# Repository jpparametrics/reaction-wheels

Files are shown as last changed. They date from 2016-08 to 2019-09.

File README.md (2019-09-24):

# THIS REPO IS NO LONGER USED. CHECK ORESAT-STRUCTURE REPO FOR CURRENT REACTION WHEEL FILES
# CubeSAT-Reaction-Wheel

Portland State University is developing Oregon’s first orbital satellite, a 2U Cubesat dubbed Oresat. This cubesat will use a reaction wheel system for attitude control and pointing of the onboard antennas and cameras. I am developing the controller, designing the structure and sourcing hardware for both the space rated system and a ground test system that will also be used for demonstration purposes. This system has been tested using the Dryden Drop Tower at PSU as well as in captive hanging tests. The current controller is a simple proportional controller, however using data collected from the drop test I will refine the model and implement a more sophisticated controller. Video of the tests can be seen at:  [Captive Controller Hanging Test](https://www.youtube.com/watch?v=Is1gPHlewtgand) and [Dryden Drop Tower Micro-Gravity Test](https://www.youtube.com/watch?v=cC2FpmCP5B4)

Both of the previous tests were conducted using a simple open loop proportional controller that was tuned via test to induce a slightly underdamped response. This was to create data that can be more easily compared to an ideal model.

CubeSat Model Comparison

## Ongoing Development

There's a Google drive folder [here](https://drive.google.com/drive/folders/0BzW5XSZ87m-TVnFDZUc1TUkwN1U?usp=sharing)

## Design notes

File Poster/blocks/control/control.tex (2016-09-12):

\documentclass[slidestop,compress]{beamer}
\usepackage[orientation=portrait,size=custom, width=30, height=25, debug]{beamerposter}
\usetheme{simple}

\usepackage{lmodern}
\usepackage[scale=2]{ccicons}

% TODO: 
%   position adjustement
%   change colours
%       

% Watermark background (simple theme)

\begin{document}

\begin{frame}[plain]
\begin{block}{\vspace{0.5 cm} 

\centering Controls Development}
\begin{columns}
	\column{.9\textwidth}
\begin{itemize}
\item The controller for the reaction wheel system is a simple PID loop 
\item The top-level controller design procedure was as follows:
\begin{enumerate}
\item Determine the transfer functions from dynamics analysis of free body diagrams of the system
\item Create simulation in GNU Octave
\item Design the controller using iterative testing (with comparisons to the model) and classical Bode techniques
\end{enumerate}
\item The forces acting on the cube are the torques created by the motors $T_i^0$, damping effects $b_1 \dot{\theta}_{cube}$, and spring effects $G_1 \theta_{cube}$. Summing the moments around the center of gravity gives the following equation (for the x-axis):

\[
\sum M_0^{+ \circlearrowleft} = I_{x,cube} \ddot{\theta}_{x,cube} = T^0_{Ax} + T^0_{Bx} - T^0_{Cx} - T^0_{Dx} + T^0_x - \dot{\theta}_{x,cube} - G_x \theta_{x,cube}.
\] 

\item By setting the system to Standard Equilibrium Position (at SEP the input perturbations are set to zero), considering only a single input, substituting the torque-inertia relation,  and taking the Laplace transform we arrive at the ({\emph{incredibly simple}}) transfer function of the cube:
\[G_A(s)=\frac{\theta_{x,cube}(s)}{\theta_A(s)}=\frac{s^2}{\cfrac{I_{x,cube}}{\sin(45^{\circ}) I_{rw}}s^2 + \cfrac{b_x}{\sin(45^{\circ}) I_{rw}}s + \cfrac{G_x}{\sin(45^{\circ}) I_{rw}}}.
\]
\end{itemize}
\end{columns}

\vspace{0.5 cm}
\end{block}    
\end{frame}

\end{document}

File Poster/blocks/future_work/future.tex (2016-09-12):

\documentclass[slidestop,compress]{beamer}
\usepackage[orientation=portrait,size=custom, width=25, height=8, debug]{beamerposter}
\usetheme{simple}

\usepackage{lmodern}
\usepackage[scale=2]{ccicons}

% TODO: 
%   position adjustement
%   change colours
%       

% Watermark background (simple theme)

\begin{document}

\begin{frame}[plain]
\begin{block}{\vspace{0.5 cm}

\centering Further Work}

\begin{columns}
\column{.9\textwidth}
\begin{itemize}
\item Need more drop-tests: complete Bode diagram to improve dynamical model, further controller design iterations
\item State determination with sensor fusion via Kalman filtering suntracker, magnetometer, and gyroscopes
\end{itemize}
\end{columns}

\vspace{0.5 cm}
\end{block}    
\end{frame}

\end{document}

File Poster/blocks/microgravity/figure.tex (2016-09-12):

\documentclass[slidestop,compress]{beamer}
\usepackage[orientation=portrait,size=custom, width=25, height=26, debug]{beamerposter}
\usetheme{simple}

\usepackage{lmodern}
\usepackage[scale=2]{ccicons}

% TODO: 
%   position adjustement
%   change colours
%       

% Watermark background (simple theme)

\begin{document}

\begin{frame}[plain]
\begin{block}{\vspace{0.5 cm}

\centering $\pmb \mu$-gravity Controls Testing}
\begin{columns}
    \column{.9\textwidth}
\begin{itemize}
\item Bode analysis of cube dynamics in ``space-like" free-fall environment
\item {\it Portland State University's} Dryden Drop Tower facility can access a 1x$10^{-5}$ to $10^{-6}$-g environment for 2.1 s
\item Cube damps roll following a random (25\% duty cycle PWM) perturbing impulse\\

\end{itemize}
\begin{figure}[!ht]
\centering
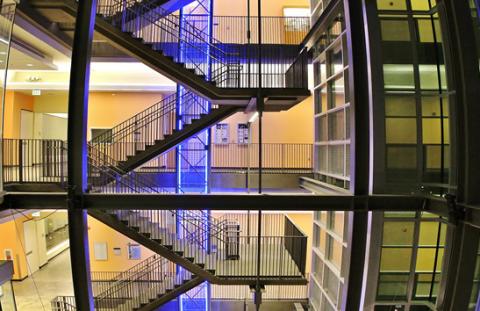
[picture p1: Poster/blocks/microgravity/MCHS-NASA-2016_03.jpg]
{
\caption{{\it Portland State University's} Dryden Drop Tower (Credit: Andrew Wollman)}

\vspace{0.5 cm}
} 
\end{figure}
\end{columns}
\end{block}    
\end{frame}

\end{document}

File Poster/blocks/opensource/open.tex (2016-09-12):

\documentclass[slidestop,compress]{beamer}
\usepackage[orientation=portrait,size=custom, width=25, height=7, debug]{beamerposter}
\usetheme{simple}

\usepackage{lmodern}
\usepackage[scale=2]{ccicons}

% TODO: 
%   position adjustement
%   change colours
%       

% Watermark background (simple theme)

\begin{document}

\begin{frame}[plain]
\begin{block}{\vspace{0.5 cm}

\centering Open-Source}
\begin{columns}
    \column{.9\textwidth}
\begin{itemize}
\item Project deliverables freely and publicly available under a GNU GPL v2 license
\item \texttt{https://github.com/oresat}
\end{itemize}
\end{columns}

\vspace{0.5 cm}
\end{block}    
\end{frame}

\end{document}

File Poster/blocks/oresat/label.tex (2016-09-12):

\documentclass[slidestop,compress]{beamer}
\usepackage[orientation=portrait,size=custom, width=27, height=15, debug]{beamerposter}
\usetheme{simple}

\usepackage{lmodern}
\usepackage[scale=2]{ccicons}

% TODO: 
%   position adjustement
%   change colours
%       

% Watermark background (simple theme)

\begin{document}

\begin{frame}[plain]
\begin{block}{\vspace{0.5 cm}

\centering OreSat}
\begin{columns}
    \column{.9\textwidth}
\begin{itemize}
\item {\bf Mission: STEM outreach by sending live video space-to-ground to tracking stations built and operated by Oregon high schools}
\item Ground stations will be built using 3D printers, COTS WiFi adapter cards, and existing augmented reality cellphone apps that track satellites
\item S-band downlink at approximately 15 dBi gain. Needs to ``point-and-stare" at ground stations with {\bf 5-10$^{\circ}$ of pointing at 1 deg/s of slew}
\item Will use a {\bf{reaction wheel}} based system to provide attitude control

\end{itemize}
\end{columns}

\vspace{0.5 cm}
\end{block}    
\end{frame}

\end{document}

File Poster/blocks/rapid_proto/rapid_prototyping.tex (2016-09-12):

\documentclass[slidestop,compress]{beamer}
\usepackage[orientation=portrait,size=custom, width=25, height=26, debug]{beamerposter}
\usetheme{simple}

\usepackage{lmodern}
\usepackage[scale=2]{ccicons}

% TODO: 
%   position adjustement
%   change colours
%       

% Watermark background (simple theme)

\begin{document}

\begin{frame}[plain]
\begin{block}{\vspace{0.5cm}

\centering Rapid Prototyping}
\begin{columns}
    \column{.9\textwidth}
\begin{itemize}
\item Designed for rapid iteration
\item FDM 3D printed main structure
\item Inexpensive COTS components: DC Brushless hobby motors, Intel Edison microcontroller, and Sparkfun ``blocks"
\item Controller code written in \emph{Python}
\end{itemize}
\begin{figure}[!ht]
\centering
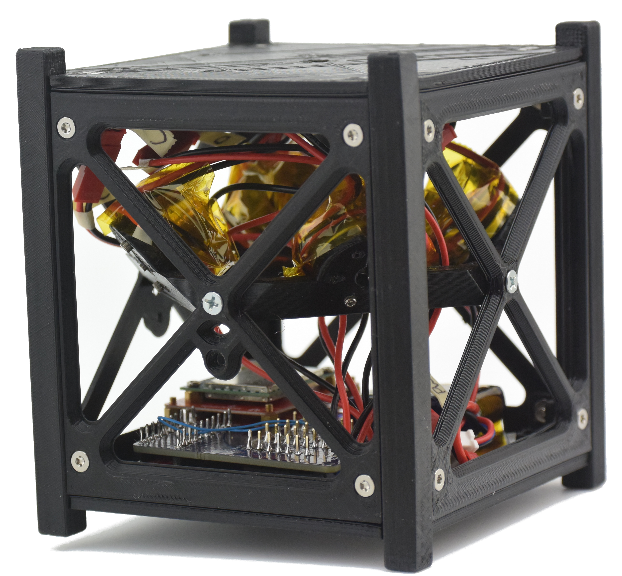
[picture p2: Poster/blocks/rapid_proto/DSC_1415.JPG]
{
\caption{The reaction wheel subsystem test cube.}
} 
\end{figure}
\end{columns}

\vspace{0.5 cm}
\end{block}    
\end{frame}

\end{document}

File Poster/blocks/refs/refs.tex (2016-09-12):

\documentclass[slidestop,compress]{beamer}
\usepackage[orientation=portrait,size=custom, width=25, height=11, debug]{beamerposter}
\usetheme{simple}

\usepackage{lmodern}
\usepackage[scale=2]{ccicons}

% TODO: 
%   position adjustement
%   change colours
%       

% Watermark background (simple theme)

\begin{document}

\begin{frame}[plain]
\begin{block}{\vspace{0.5 cm}

\centering References}
\begin{columns}
    \column{.9\textwidth}
\begin{thebibliography}{9}
\bibitem{Mahoney:15bk}
Mahoney, Erin. {\it CubeSat Launch Initiative: 50 CubeSats from 50 States in 5 Years.} NASA, April 9, 2015. http://www.nasa.gov/content/cubesat-launch-initiative-50-cubesats-from-50-states-in-5-years.\\

\bibitem{Cubesat:14bk}
The CubeSat Program, {\it Cal Poly SLO. CubeSat Design Specification Rev. 13.} San Luis
Obispo: California Polytechnic State University; 2014.
\end{thebibliography}
\end{columns}

\vspace{0.5 cm}
\end{block}    
\end{frame}

\end{document}

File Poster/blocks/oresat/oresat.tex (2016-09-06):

\documentclass[slidestop,compress]{beamer}
\usepackage[orientation=portrait,size=custom, width=11, height=1.1, debug]{beamerposter}
\usetheme{simple}

\usepackage{lmodern}
\usepackage[scale=2]{ccicons}

% TODO: 
%   position adjustement
%   change colours
%       

% Watermark background (simple theme)

\begin{document}

\begin{frame}[plain]
$\mu$-gravity attitude control test    
\end{frame}

\end{document}

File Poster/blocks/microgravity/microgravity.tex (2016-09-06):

\documentclass[slidestop,compress]{beamer}
\usepackage[orientation=portrait,size=custom, width=25, height=20, debug]{beamerposter}
\usetheme{simple}
\usepackage{svg}

\usepackage{lmodern}
\usepackage[scale=2]{ccicons}

% TODO: 
%   position adjustement
%   change colours
%       

% Watermark background (simple theme)

\begin{document}

\begin{frame}[plain]

\includesvg[width=0.9\linewidth]{Gyro_Data_vs_Model_v2}
    
\end{frame}

\end{document}

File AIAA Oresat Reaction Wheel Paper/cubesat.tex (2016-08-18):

% `template.tex', a bare-bones example employing the AIAA class.
%
% For a more advanced example that makes use of several third-party
% LaTeX packages, see `advanced_example.tex', but please read the
% Known Problems section of the users manual first.
%
% Typical processing for PostScript (PS) output:
%
%  latex template
%  latex template   (repeat as needed to resolve references)
%
%  xdvi template    (onscreen draft display)
%  dvips template   (postscript)
%  gv template.ps   (onscreen display)
%  lpr template.ps  (hardcopy)
%
% With the above, only Encapsulated PostScript (EPS) images can be used.
%
% Typical processing for Portable Document Format (PDF) output:
%
%  pdflatex template
%  pdflatex template      (repeat as needed to resolve references)
%
%  acroread template.pdf  (onscreen display)
%
% If you have EPS figures, you will need to use the epstopdf script
% to convert them to PDF because PDF is a limmited subset of EPS.
% pdflatex accepts a variety of other image formats such as JPG, TIF,
% PNG, and so forth -- check the documentation for your version.
%
% If you do *not* specify suffixes when using the graphicx package's
% \includegraphics command, latex and pdflatex will automatically select
% the appropriate figure format from those available.  This allows you
% to produce PS and PDF output from the same LaTeX source file.
%
% To generate a large format (e.g., 11"x17") PostScript copy for editing
% purposes, use
%
%  dvips -x 1467 -O -0.65in,0.85in -t tabloid template
%
% For further details and support, read the Users Manual, aiaa.pdf.

% Try to reduce the number of latex support calls from people who
% don't read the included documentation.
%
\typeout{}\typeout{If latex fails to find aiaa-tc, read the README file!}
%

\documentclass[]{aiaa-tc}% insert '[draft]' option to show overfull boxes
\usepackage{amssymb}
\usepackage{amsmath}
\usepackage{svg} 

 \title{An Open-Source Reaction Wheel System for Oregon's First Satellite}

 \author{
  Jeremy A. Louke%
  	\thanks{Student BScME, Maseeh College of Engineering, Portland State University, Student Member.}\\
  {\normalsize\itshape
   Portland State Aerospace Society, Portland, OR, 97201}\\
  \and
  Erin S. Schmidt% 
  	\thanks{Student MSME, Maseeh College of Engineering, Portland State University, Student Member. esch2@pdx.edu} \ \
  Calvin J. Young\thanksibid{1}\\
  {\normalsize\itshape
  Portland State University, Portland, OR, 97201}
 }

 % Data used by 'handcarry' option if invoked
 \AIAApapernumber{YEAR-NUMBER}
 \AIAAconference{Conference Name, Date, and Location}
 \AIAAcopyright{\AIAAcopyrightD{YEAR}}

 % Define commands to assure consistent treatment throughout document
 \newcommand{\eqnref}[1]{(\ref{#1})}
 \newcommand{\class}[1]{\texttt{#1}}
 \newcommand{\package}[1]{\texttt{#1}}
 \newcommand{\file}[1]{\texttt{#1}}
 \newcommand{\BibTeX}{\textsc{Bib}\TeX}

\begin{document}

\maketitle

\begin{abstract}
Portland State University is developing Oregon's first orbital satellite, a 2U CubeSat, dubbed Oresat. One of the primary missions of this CubeSat is to be a vehicle for STEM outreach by sending live video space-to-ground to tracking stations built and operated by Oregon high schools. This CubeSat will use a reaction wheel system for attitude control and pointing of the onboard camera, and high-gain antenna. Details of the development of the reaction wheel ground test article, and its controller, are presented here. We also present preliminary results of attitude control testing conducted in the brief (2.1 s) free-fall environment of Portland State University's Dryden Drop Tower. 
\end{abstract}

\section*{Nomenclature}

\begin{center}
\parbox{0cm}
{\begin{tabbing}
  XXX \= \kill% this line sets tab stop
  $M_0^{+ \circlearrowleft}$ \qquad Moment in the x-axis (N m)\\
  $T^0$ \qquad Torque (N m)\\
  $\theta$ \qquad Angular position (${}^{\circ}$)\\
  $\dot{\theta}$ \qquad Angular velocity (${}^{\circ}/s$)\\ 
  $\ddot{\theta}$ \qquad Angular acceleration (${}^{\circ}/s^2$) \\
  $I$ \qquad Moment of Inertia (N $\textrm{m}^2$)\\
  $b$ \qquad Damping Coefficient (N s/m)\\ 
  $G$ \qquad Spring Coefficient (N/m)\\
  $COTS$ \qquad Commercial Off-The-Shelf\\
  $FDM$ \qquad Fused Deposition Modeling\\
  $IMU$ \qquad Inertial Measurement Unit\\
  $PWM$ \qquad Pulse Width Modulation\\ \\
  \textit{Subscripts}\\
  $x$ \qquad Index for Cartesian axes \\
  $rw$\qquad Reaction Wheel\\
  $n$ \qquad Motor Index\\
  $A, B, C, D$ \qquad Indices for Motors A, B, C, and D\\
 \end{tabbing}}
 \end{center}
 
\section{Introduction}
Small educational satellites have been launched by dozens of universities around the United States as part of NASA’s CubeSat Launch Initiative (CLSI), especially under the auspices of the Educational Launch of Nanosatellites (ELaNa) program. As of 2015 CubeSats from 29 states have flown under the program, however the great state of Oregon has yet to join their ranks\cite{Mahoney:15bk}. During the summer of 2015 the Oresat project was initiated by the Portland State Aerospace Society (PSAS) to rectify this situation. PSAS is an engineering student organization and citizen science project located at Portland State University dedicated to developing low-cost, open-source, and open-hardware high-powered rockets and avionics systems with special interests in venture class launch vehicle technologies and nanosatellites\cite{PSAS:15bk}.

The Oresat satellite will follow the ``2U" CubeSat standard \cite{Cubesat:14bk}. A CAD render of the Oresat concept is pictured in Figure \ref{fig:oresat}. The primary objectives of the project are to test several subsystems in the environment of a 400 km circular Low Earth Orbit: the ``Low Gain Radio (LGR)" communication board and the highly tolerant ``System Controller" board. The LGR is the main low-gain radio system based on a 436 MHz radio system using the MKW01Z128 microcontroller. The System Controller is being designed expressly for the space environment, and will include some measure of fault-tolerance and radiation hardening.

The secondary mission goal is to run an educational outreach project in the state of Oregon. Called ``DxWiFi", after the Amateur Radio ``Dx" code for distance, OreSat will broadcast a live video feed from space to the ground using the standard 2.4 GHz  802.11b ``WiFi" protocol. DxWiFi ground stations will be built by Oregon high schools using 3D printers, COTS WiFi adapter cards, and existing augmented reality cellphone apps that track satellites.

A severely power limited ($\sim$ 1 W) S-band downlink from LEO unfortunately requires high gain antennas, both on the ground and on the space vehicle. However, in order to minimize required deployables on the space vehicle, and to provide for the general simplicity of design, construction, and operation of future ground stations, we chose a 16 turn helical with approximately 15 dBi gain. This gives a relatively broad beam width antenna, requiring pointing, but only on the order of a 5-10 degrees. Since nadir pointing will only allow a few seconds of data link, Oresat must ``point and stare" at a ground station that has requested to download video. This degrees-per-second slew of the antenna (and camera) requires rapid pointing changes that magnetorquers simply can not provide. Following from this is the need for a robust system to provide attitude control for Oresat. This system will be reaction wheel based. Per PSAS’s open-source ethos all (non-ITAR) project development deliverables are being made freely and publicly available under a GNU GPL v2 license\cite{Oresat:15bk}. It is hoped by the authors, and the members of PSAS that the discourse around educational CubeSats and their design will be elevated by making the information for this project publicly available.

\begin{figure}[h!]
  \centering
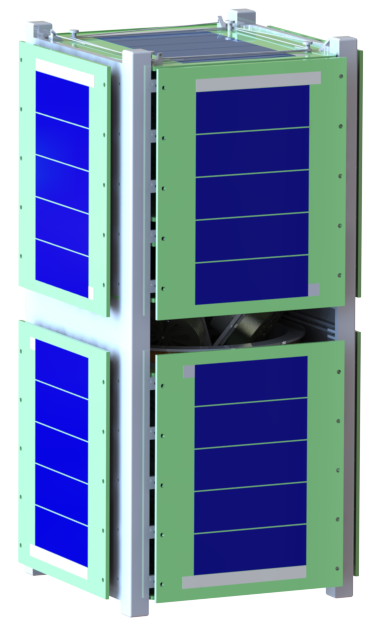
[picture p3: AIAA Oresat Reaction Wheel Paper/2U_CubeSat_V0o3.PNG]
  
  \caption{Speculative mockup in SolidWorks of the 2U Oresat chassis.}
  \label{fig:oresat}
\end{figure}

\section{Concept Definition}
	Angular rate and pointing precision requirements for the flight attitude control system are determined from orbital parameters (likely those offered by Nanoracks deployment from the ISS) and the expected performance of the PSAS DxWiFi telemetry system. The ground test article is a proof of concept and uses inexpensive COTS DC brushless motors which are significantly more powerful than those required for the flight use case. The ground test article is broadly similar in design to the flight system, for example by using 4 momentum-wheels in a pyramid configuration for added redundancy and on-orbit mission assurance. Such a design is similar one recently developed for a master's thesis project at California Polytechnic State University San Luis Obispo\cite{Logan:08bk}. On Oresat a magnetorquer will be used to periodically desaturate the reaction wheels by dumping accumulated momentum into the Earth's magnetic field. The other principle difference between the ground test and flight designs is that the ground test article uses the 1U form factor whereas Oresat is planned to be 2U.

\section{Design and Fabrication}
	The Oresat reaction wheel system chassis was developed using rapid prototyping techniques over a short time period (approximately 8 weeks). This approach enables rapid design iteration cycles. A mockup 1U CubeSat structure was drafted in SolidWorks CAD, and fabricated using an FDM 3D printer. Mounted on the 3D-printed chassis are the 4X DC brushless motors, a 4-cell Li-Po battery pack, IMU shield, Intel Edison microcontroller and accompanying GPIO breakout. This `ground' test article is shown in Figure \ref{fig:rcs}. As previously noted there are several departures in the design of the ground test article from the flight system. Among these are the COTS DC brushless motors used to drive the momentum wheels; having a very high RPM limit, specifically 22,000 RPM, these motors provide substantially more torque, shaft power, and shaft speed than required by the flight system. The use of such motors is justified by the need to ground test the controllers ability to react quickly to perturbations, and to test the limits of the controller rise time. In practice, the ground test article is not constrained by requirements for power consumption, or heat generation as the flight system surely will be. 

\begin{figure}[h!]
  \centering
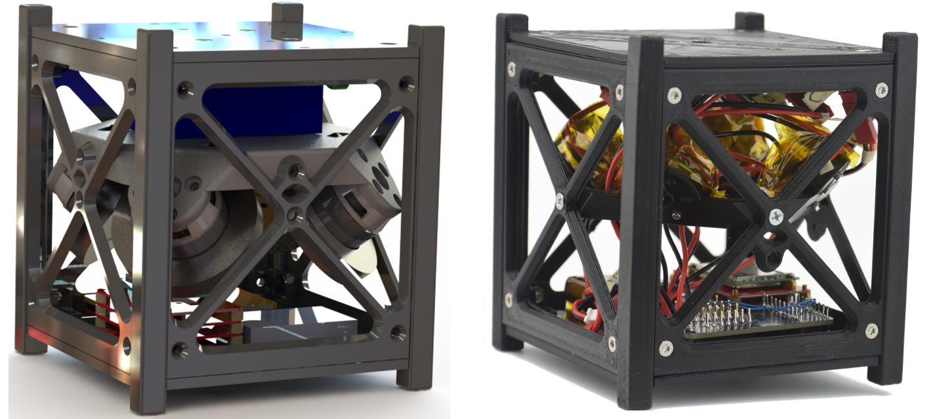
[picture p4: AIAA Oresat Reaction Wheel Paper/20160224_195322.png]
  
  \caption{Reaction wheel ground test articles: a CAD render in SolidWorks, and the completed prototype.}
  \label{fig:rcs}
\end{figure}

\section{Controls Simulation and Design}
The controller for the reaction wheel system is a Proportional-Integral loop implemented on an Intel Edison with code written in Python. The Edison receives feedback from a 9-DoF IMU over analog-in, and sends signals via GPIO to the motors. The top-level controller design procedure was as follows:
\begin{enumerate}
\item Determine the transfer functions from dynamics analysis of free body diagrams of the system
\item Create simulation in GNU Octave
\item Design the controller using iterative testing (with comparisons to the model) and classical Bode techniques
\end{enumerate}
The transfer functions are determined with a dynamics analysis of the free body diagram, shown schematically for a single axis in Figure \ref{fig:FBD}. The forces acting on the cube are the torques created by the motors $T_i^0$, damping effects $b_1 \dot{\theta}_{cube}$, and spring effects $G_1 \theta_{cube}$. Summing the moments around the center of gravity gives the following equation:\\

\begin{equation}
\label{eq:moment}
\sum M_0^{+ \circlearrowleft} = I_{x,cube} \ddot{\theta}_{x,cube} = T^0_{Ax} + T^0_{Bx} - T^0_{Cx} - T^0_{Dx} + T^0_x - \dot{\theta}_{x,cube} - G_x \theta_{x,cube}.
\end{equation}\\
	
Solving Eqn. \ref{eq:moment} so that $\theta_{cube}$ and its derivatives are on the left side, and the motor torques are on the right side, as well as setting the system to Standard Equilibrium Position (at SEP the input perturbations are set to zero) and substituting the torque-inertia relation we have\\

\[
T^0_x = 0,
\]
\[
T^0_{nx} = I_{rw}\ddot{\theta}_n.\]\\

This gives us the following equation:\\
 
\[
I_{x,cube} \alpha_x + b_x \dot{\theta}_{x,cube} + G_x \theta_{x,cube} = \sin(45^{\circ}) I_{rw} (\ddot{\theta}_A + \ddot{\theta}_B -\ddot{\theta}_C - \ddot{\theta}_D).
\]\\	
Per the textbook definition of a transfer function we have the output of a system with respect to a single input, so all motors are set to zero except for one (A for this example). Applying a Laplace transform to the previous equation we have\\

\[
\frac{I_{x,cube}}{\sin(45^{\circ}) I_{rw}} \theta_{x,cube} s^2 +
\frac{b_x}{\sin(45^{\circ}) I_{rw}} \theta_{x,cube} s +
\frac{G_x}{\sin(45^{\circ}) I_{rw}} \theta_{x,cube} = \theta_A s^2.
\]\\
	
Finally moving $\theta_{cube}$ and $\theta_A$ to the left side of the equation and everything else to the right, we arrive at the transfer function describing the system:\\

\begin{equation}
\label{eq:xfer}
G_A(s)=\frac{\theta_{x,cube}(s)}{\theta_A(s)}=\frac{s^2}{\cfrac{I_{x,cube}}{\sin(45^{\circ}) I_{rw}}s^2 + \cfrac{b_x}{\sin(45^{\circ}) I_{rw}}s + \cfrac{G_x}{\sin(45^{\circ}) I_{rw}}}.
\end{equation}\\
	
Using the transfer functions, given schematically for one axis by Eqn. \ref{eq:xfer}, a simulation was created in GNU Octave which yielded step response plots shown in Figure \ref{fig:simulation}. The simulation model will further aid in Bode analysis for the determination of stability margins which relate the frequency response of the system to its time response. The margins can be adjusted with the use of a controller to affect the time response characteristics of the system. In the case of the ground test system we expect the rise time for a $90^{\circ}$ step input to be under 1 second. 
\begin{figure}[h!]
  \centering
  \includesvg[width=0.35\linewidth]{FBD}
  \caption{Free Body Diagram of the CubeSat in the Cartesian x-axis.}
  \label{fig:FBD}
\end{figure}

\begin{figure}[h!]
  \centering
  {\footnotesize \includesvg[width=0.9\linewidth]{motor_torque}}
  \caption{CubeSat step response compared with singular motor response.}
  \label{fig:simulation}
\end{figure}

\begin{figure}[!ht]
 \centering
 {\includesvg[width=0.9\linewidth]{drop_test}}
 \caption{Time lapse of the CubeSat controller drop tower test. Initial roll impulse damped to 0 rad/s in approximately 1.9 s. The light green dot locates a fixed reference point on the CubeSat chassis. The rotation of the CubeSat, as viewed from above, is clockwise. The CubeSat is also translating upwards at approximately 7 cm/s.}
 \label{fig:lapse}
\end{figure}

\begin{figure}[!ht]
 \centering
 {\footnotesize \includesvg[width=0.9\linewidth]{Gyro_Data_vs_Model}}
 \caption{Drop tower test 1-DoF gyro data for z-angular rates (in pink) compared to the rates predicted by the controller model (in blue). The gyro data is presented here in an unfiltered form.}
 \label{fig:drop_results}
\end{figure}

\section{Controller Testing and Results}
A unique and exciting testing opportunity involves exploiting the high-quality $\mu$-gravity environment of Portland State University's Dryden Drop Tower (DDT) facility for free fall tests of the reaction wheel system. The Dryden Drop Tower, patterned on the 2.2 Second Drop Tower facility at NASA's Glenn Research Center in Cleveland, Ohio, is optimized for exceptionally fast drop turnaround times. The DDT is one of the most productive drop towers in the world for its class, with more than 5800 drops over its 6 year history. 
The DDT's 2.1 seconds of free-fall conditions provide unique opportunities for the observation of phenomena that are usually masked at the macro-scale in 1-g gravity fields. The relative quality of the $\mu$-gravity environment of a drop tower is very high compared to those offered by parabolic flights (generally $10^{-5}$ or $10^{-6}$-g for the drop tower compared to $10^{-1}$ or $10^{-2}$-g for a parabolic flight). In this relatively high quality $\mu$-gravity the CubeSat attitude control system can be tested in an environment similar to that of outer space (at least in an inertial sense). In the DDT the reaction wheel system testing program involved a random (25 \% duty cycle PWM) perturbing impulse followed by a command to damp this roll in the brief Cinderella-like moment before 1-g gravity returns 2.1 seconds later. A time lapse image of the CubeSat, showing the initial roll impulse and subsequent damping is presented in Figure \ref{fig:lapse}. On a qualitative examination of the simulated roll response compared to the experimental gyro rates from the IMU, the model appears to in strong agreement (in terms of the frequency and damping ratio) with the actual physical system, at least for this particular impulse. This is shown in Figure \ref{fig:drop_results}. The 0.03 s phase shift between the gyro data and the angular rates predicted by the simulation may be due to the discrete time lag of the physical controller, and also to the small amount of damping by aerodynamic drag.  

Following from the first test, an initial modicum of model validation allows us to continue with the model as the basis for further iterative controls testing. We plan to select a series of additional test points to formulate a more complete Bode diagram; this will require drop tests at several additional frequencies. Once the Bode diagram is completed a new model can be backed out, and the iterative controller design loop can be started anew. This work is in progress (as of August, 2016), and should be completed before the Oresat Critical Design Review in November, 2016 which is concurrent with the next round of NASA ELaNa proposals.

\section{Acknowledgments}
We are indebted to PSU mechanical engineering undergraduates Marie House, and Alex Farias, for their assistance with testing the prototype, and to Brentley Wiles for the assistance he rendered with early development at the inception of this project. We are further indebted to the PSU's Dryden Drop Tower lab and the Lab for Interconnected Devices for their support both in fabricating and testing this prototype. We acknowledge PSAS's faculty mentor, Andrew Greenberg, for his support and advice. Finally, we appreciate the support of the community of PSAS crowdfunding backers for helping to translate `citizen science' from a abstract ideal into a well realized actuality, and for additionally helping to translate some starry-eyed STEM student's dreams of space into Oregon's first orbital satellite.

\begin{thebibliography}{9}% maximum number of references (for label width)

\bibitem{Mahoney:15bk}
Mahoney, Erin. {\it CubeSat Launch Initiative: 50 CubeSats from 50 States in 5 Years.} NASA, April 9, 2015. http://www.nasa.gov/content/cubesat-launch-initiative-50-cubesats-from-50-states-in-5-years.\\

\bibitem{PSAS:15bk}
{\it Portland State Aerospace.} PSAS. Accessed February 25, 2016. http://psas.pdx.edu.\\

\bibitem{Cubesat:14bk}
The CubeSat Program, {\it Cal Poly SLO. CubeSat Design Specification Rev. 13.} San Luis
Obispo: California Polytechnic State University; 2014.\\

\bibitem{Oresat:15bk}
{\it Oregon Small Satellite Project.} GitHub. Accessed February 25, 2016. https://github.com/oresat.\\

\bibitem{Logan:08bk}
Logan, Jeffery. {\it Control and Sensor Development on a Four-Wheel Pyramidal Reaction Wheel Platform,} Master’s Thesis, California Polytechnic State University, San Luis Obispo, 2008.\\

\end{thebibliography}

\end{document}

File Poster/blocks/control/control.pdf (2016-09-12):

Controls Development

I The controller for the reaction wheel system is a simple PID loop
I The top-level controller design procedure was as follows:

### 1. Determine the transfer functions from dynamics analysis of free body diagrams of the

system

### 2. Create simulation in GNU Octave 3. Design the controller using iterative testing (with comparisons to the model) and

classical Bode techniques
I The forces acting on the cube are the torques created by the motors T

0
i

,
damping effects b1

˙θcube, and spring effects G1θcube. Summing the moments around the center of gravity gives the following equation (for the x-axis):

X M

+
0 = Ix,cube ¨θx,cube = T

0
| Ax+T

0
Bx−T

0
Cx−T

0
Dx+T

0
x − ˙θx,cube−Gxθx,cube.

I By setting the system to Standard Equilibrium Position (at SEP the input perturbations are set to zero), considering only a single input, substituting the torque-inertia relation, and taking the Laplace transform we arrive at the (incredibly simple) transfer function of the cube:

GA(s) = θx,cube(s)
θA(s)

=

s

2

| Ix,cube
sin(45◦)Irw

s

2 +

bx
sin(45◦)Irw

s +

Gx
sin(45◦)Irw

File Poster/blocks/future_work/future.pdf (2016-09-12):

Further Work

I Need more drop-tests: complete Bode diagram to improve dynamical model, further controller design iterations
I State determination with sensor fusion via Kalman filtering suntracker, magnetometer, and gyroscopes

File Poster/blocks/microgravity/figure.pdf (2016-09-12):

µ-gravity Controls Testing

I Bode analysis of cube dynamics in “space-like” free-fall environment
I Portland State University’s Dryden Drop Tower facility can access a 1x10⁻⁵

to 10⁻⁶
-g environment for 2.1 s
I Cube damps roll following a random (25% duty cycle PWM) perturbing impulse

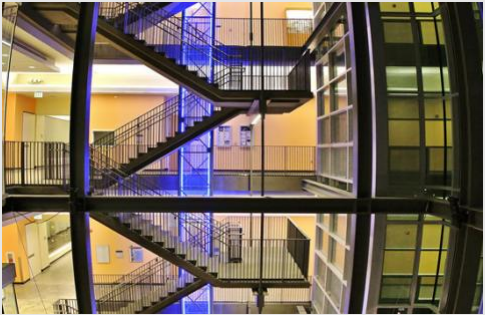
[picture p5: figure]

Figure: Portland State University’s Dryden Drop Tower (Credit: Andrew Wollman)

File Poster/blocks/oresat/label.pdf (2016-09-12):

OreSat

I Mission: STEM outreach by sending live video space-to-ground to tracking stations built and operated by Oregon high schools
I Ground stations will be built using 3D printers, COTS WiFi adapter cards, and existing augmented reality cellphone apps that track satellites
I S-band downlink at approximately 15 dBi gain. Needs to “point-and-stare” at ground stations with 5-10◦ of pointing at

### 1 deg/s of slew

I Will use a reaction wheel based system to provide attitude control

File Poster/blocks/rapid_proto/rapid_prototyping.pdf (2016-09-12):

Rapid Prototyping

I Designed for rapid iteration
I FDM 3D printed main structure
I Inexpensive COTS components: DC Brushless hobby motors, Intel Edison microcontroller, and Sparkfun “blocks”
I Controller code written in Python

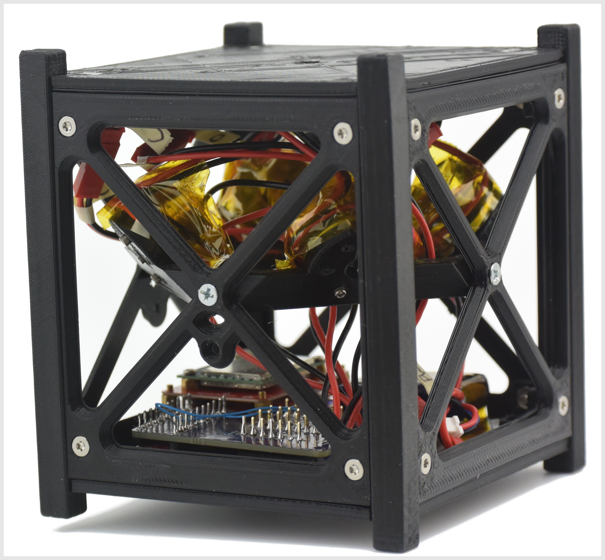
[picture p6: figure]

Figure: The reaction wheel subsystem test cube.

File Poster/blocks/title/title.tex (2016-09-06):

\documentclass[slidestop,compress]{beamer}
\usepackage[orientation=portrait,size=custom, width=25, height=8, debug]{beamerposter}
\usetheme{simple}

\usepackage{lmodern}
\usepackage[scale=2]{ccicons}

% TODO: 
%   position adjustement
%   change colours
%       

% Watermark background (simple theme)

\title{An Open-Source Reaction Wheel System for Oregon's First Satellite}
\subtitle{}
%\date{\today}
\author{
  Jeremy A. Louke%
  	%\thanks{Student BScME, Maseeh College of Engineering, Portland State University, Student Member.}\\
  %{\normalsize\itshape Portland State Aerospace Society, Portland, OR, 97201}\\
  \and
  Erin S. Schmidt% 
  	%\thanks{Student MSME, Maseeh College of Engineering, Portland State University, Student Member. esch2@pdx.edu} \ \
  	\and
  Calvin J. Young %\thanksibid{1}\\
  %{\normalsize\itshape Portland State University, Portland, OR, 97201}
 }
\institute{Portland State University}

\begin{document}

\maketitle

\end{document}

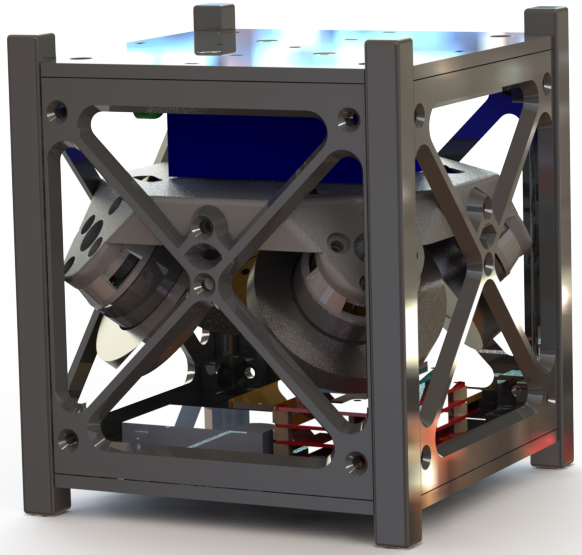
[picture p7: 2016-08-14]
AIAA Oresat Reaction Wheel Paper/Proto cube render.png

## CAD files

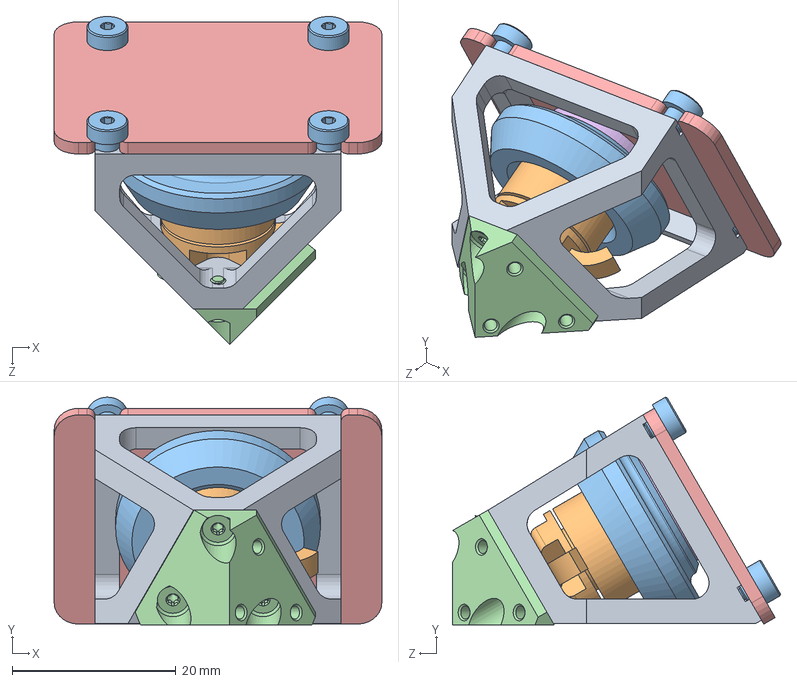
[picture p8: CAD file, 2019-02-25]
wheelUnit.SLDASM
40.0 x 27.8 x 40.0 mm
motorBracket
D1104-4000KV_rough
wheel
wedge
encoderBoard
magnetCap
magnet
M2x0.4x4_flatHead_phillips_91698A200_METRIC 18-8 SS FLAT HEAD PHIL MACHINE SCREW x 4
M2x0.4x6_flatHead_hex_brass_97595A277_BRASS HEX DRIVE FLAT HEAD SCREW x 2
sensorStandin
M2x0.4x4_2x3shoulderScrew_90263A111_316 STAINLESS STEEL PRECISION SHOULDER SCREW x 4
M2x0.4x5_flatHead_torx_92703A144_STAINLESS STEEL TORX FLAT HEAD SCREWS x 3

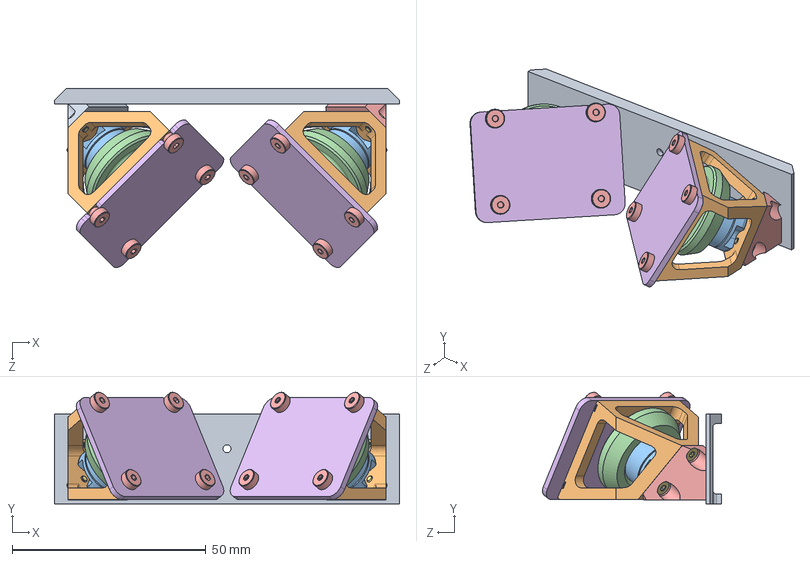
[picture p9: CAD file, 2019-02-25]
mountingBeam.SLDASM
89.0 x 28.8 x 46.2 mm
mountingBeam
motorBracket x 2
D1104-4000KV_rough x 2
wheel x 2
wedge
encoderBoard x 2
magnetCap x 2
magnet
M2x0.4x4_flatHead_phillips_91698A200_METRIC 18-8 SS FLAT HEAD PHIL MACHINE SCREW x 4
M2x0.4x6_flatHead_hex_brass_97595A277_BRASS HEX DRIVE FLAT HEAD SCREW x 2
sensorStandin
M2x0.4x5_buttonHead_91239A701_CLASS 10.9 STL BUTTON-HEAD SOCKET CAP SCREW x 4
M2x0.4x4_2x3shoulderScrew_90263A111_316 STAINLESS STEEL PRECISION SHOULDER SCREW x 8
No2-56_ultra-lowShoulderScrew_90318A101_ULTRA-LOW-PROFILE PRECISION SHOULDER SCREW x 4
M2x0.4x5_flatHead_torx_92703A144_STAINLESS STEEL TORX FLAT HEAD SCREWS x 6
M2.5x0.45x4_flatHex_91294A473_BLK-OXIDE ALLOY STL HEX DRIVE FLAT HEAD SCREW x 6
wedge_enantio

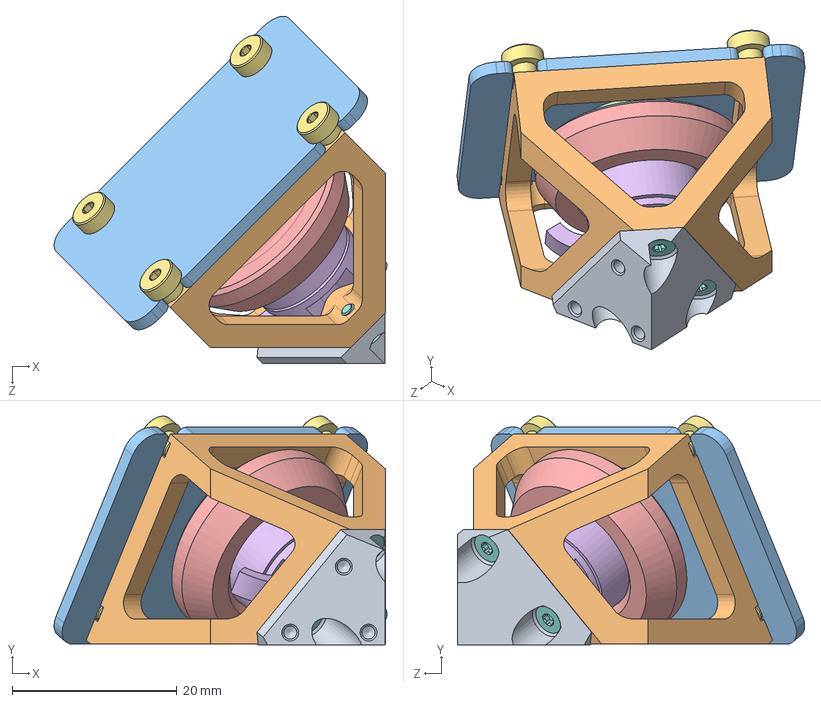
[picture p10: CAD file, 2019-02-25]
wheelUnit_enantio.SLDASM
40.4 x 27.8 x 42.2 mm
wedge_enantio
motorBracket
encoderBoard
magnetCap
wheel
D1104-4000KV_rough
M2x0.4x4_2x3shoulderScrew_90263A111_316 STAINLESS STEEL PRECISION SHOULDER SCREW x 4
M2x0.4x5_flatHead_torx_92703A144_STAINLESS STEEL TORX FLAT HEAD SCREWS x 3

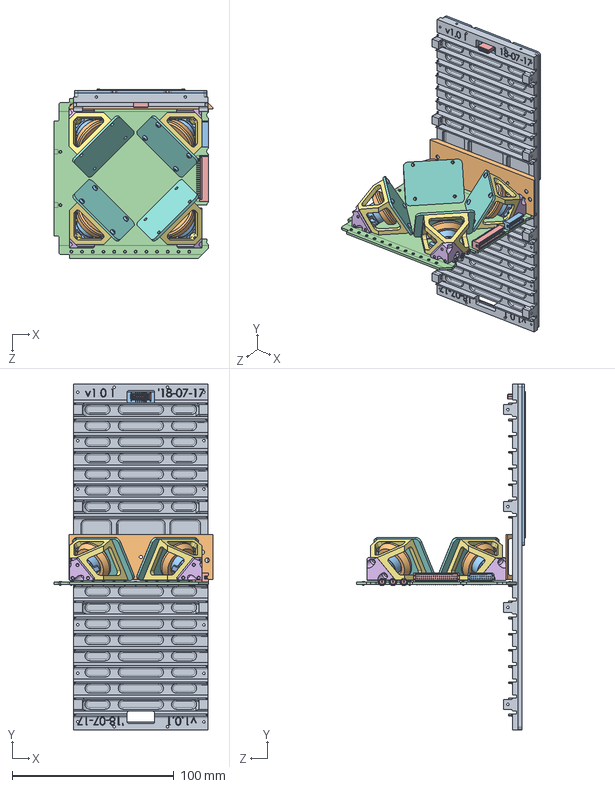
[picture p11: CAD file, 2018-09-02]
mountingExample.SLDASM
98.1 x 214.0 x 104.5 mm
Cuberail_side
mountingBeam
Solar_board
ALTA-FIVE-CELL-THROUGH-SLOT
12pin_connector
wedge_enantio x 2
motorBracket x 4
encoderBoard x 4
magnetCap x 4
wheel x 4
D1104-4000KV_rough x 4
GenericCard_board
_TFM_120_01_L_D_RA_terminal_2
_TFM_120_01_L_D_RA_pins_4
mill-max-0965-0-15-20-80-14-11-0_6995-0 x 26
mill-max-0965-0-15-20-80-14-11-0_9318-0 x 26
mill-max-0965-0-15-20-80-14-11-0_9305-0 x 26
mill-max-0965-0-15-20-80-14-11-0_SPRING x 26
_TFM_110_01_L_D_RA_terminal_2
_TFM_110_01_L_D_RA_pins_4
ACX2517-ND x 3
wedge x 2
magnet x 2
M2x0.4x4_flatHead_phillips_91698A200_METRIC 18-8 SS FLAT HEAD PHIL MACHINE SCREW x 8
M2x0.4x6_flatHead_hex_brass_97595A277_BRASS HEX DRIVE FLAT HEAD SCREW x 4
sensorStandin x 2
M2x0.4x5_buttonHead_91239A701_CLASS 10.9 STL BUTTON-HEAD SOCKET CAP SCREW x 8

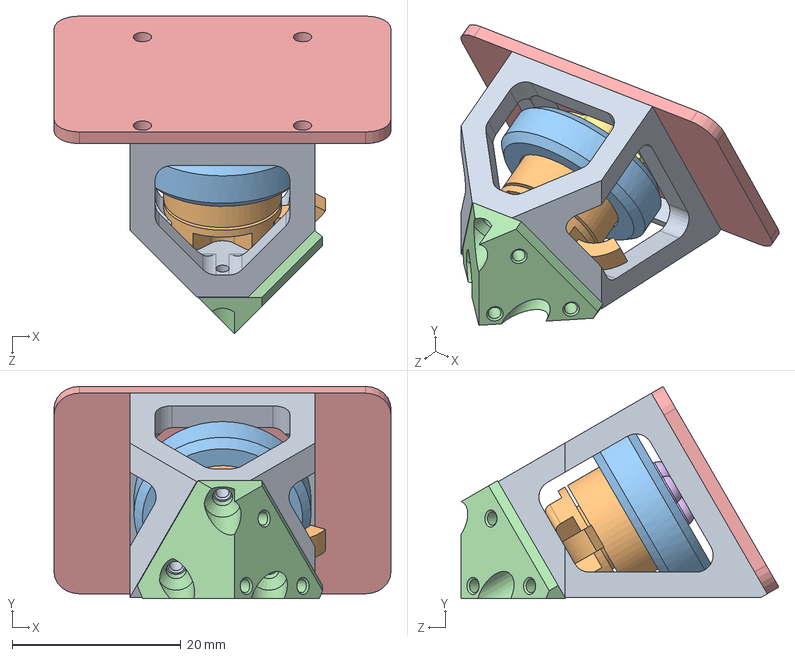
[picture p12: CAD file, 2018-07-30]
wheelUnit_cage.SLDASM
40.0 x 25.2 x 37.7 mm
motorBracket_cage
D1104-4000KV_rough
wheel
wedge_cage
encoderBoard_cage
M2x0.4x5_buttonHead_91239A701_CLASS 10.9 STL BUTTON-HEAD SOCKET CAP SCREW x 4
magnetCap
magnet

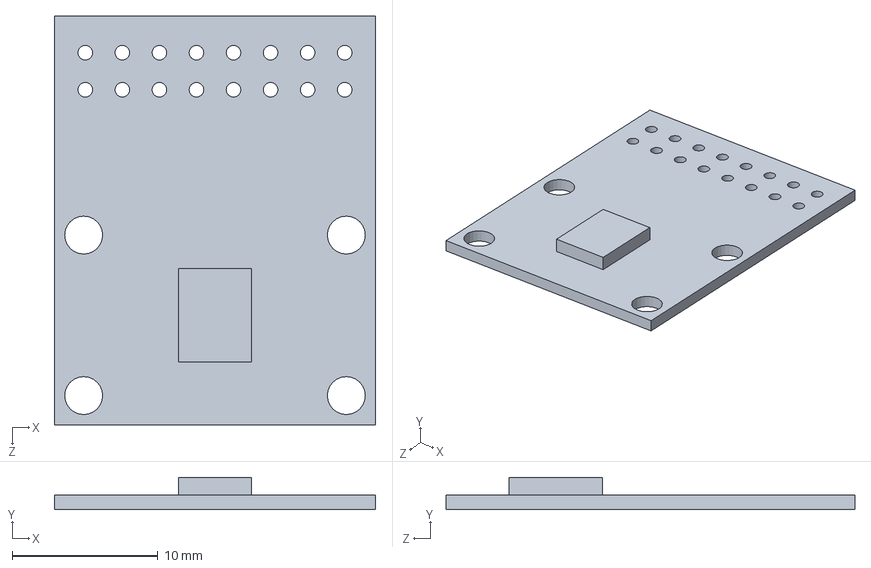
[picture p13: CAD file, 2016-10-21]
SW_CAD_1U_cubesat/ams_eval_board/ams5147_adapter_board.SLDPRT
22.0 x 2.20 x 28.0 mm

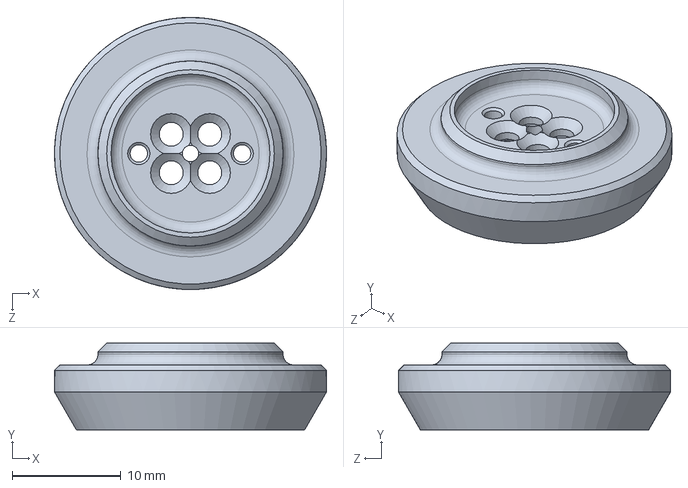
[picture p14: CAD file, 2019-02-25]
wheel.SLDPRT
25.0 x 7.95 x 25.0 mm

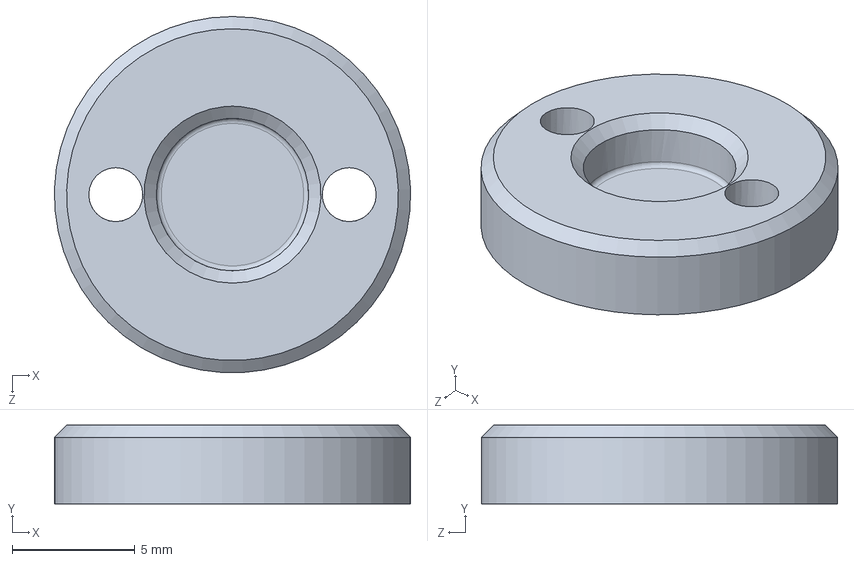
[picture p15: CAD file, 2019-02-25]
magnetCap.SLDPRT
14.5 x 3.20 x 14.5 mm

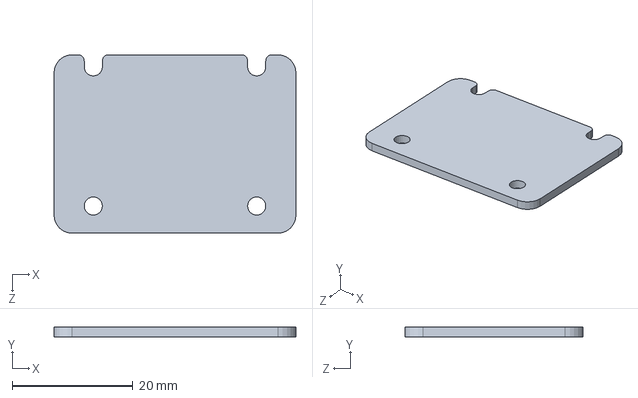
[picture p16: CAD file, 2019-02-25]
encoderBoard.SLDPRT
40.0 x 1.60 x 29.5 mm

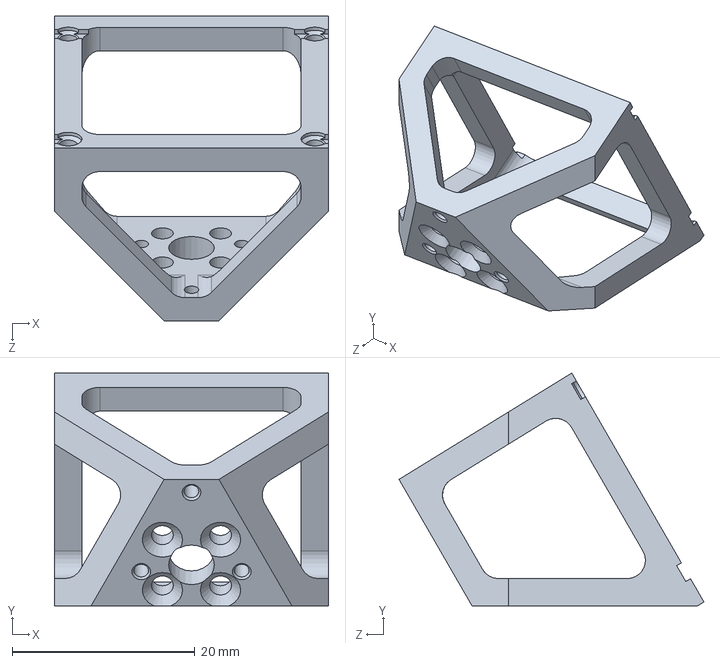
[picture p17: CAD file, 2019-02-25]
motorBracket.SLDPRT
30.0 x 25.5 x 33.4 mm

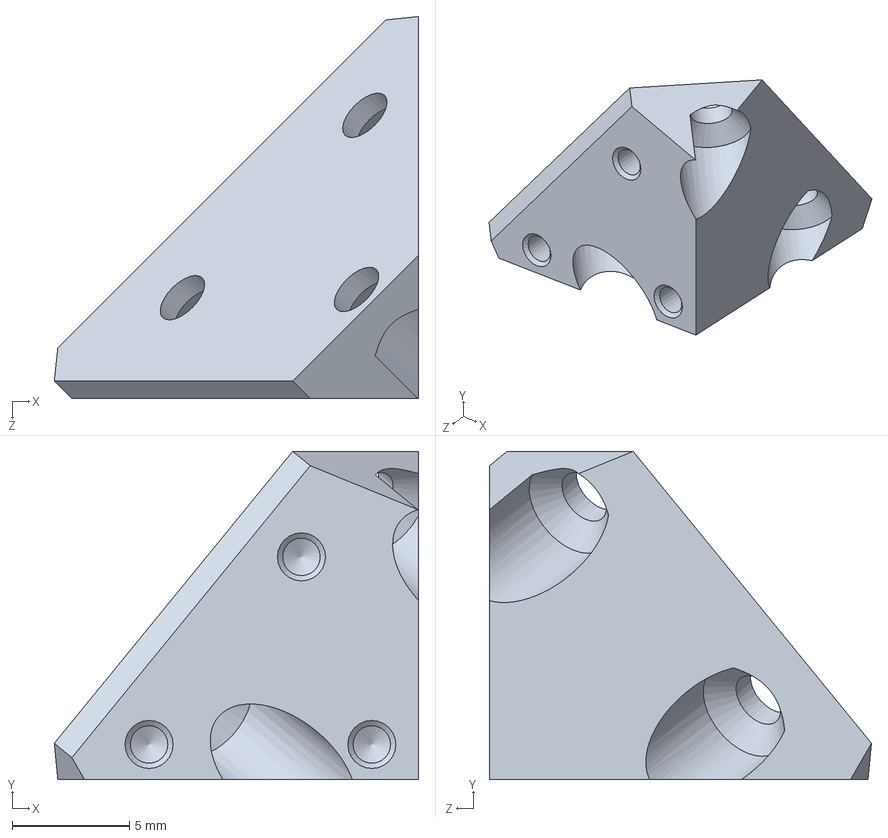
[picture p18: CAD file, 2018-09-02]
wedge_enantio.SLDPRT
15.5 x 14.0 x 16.3 mm

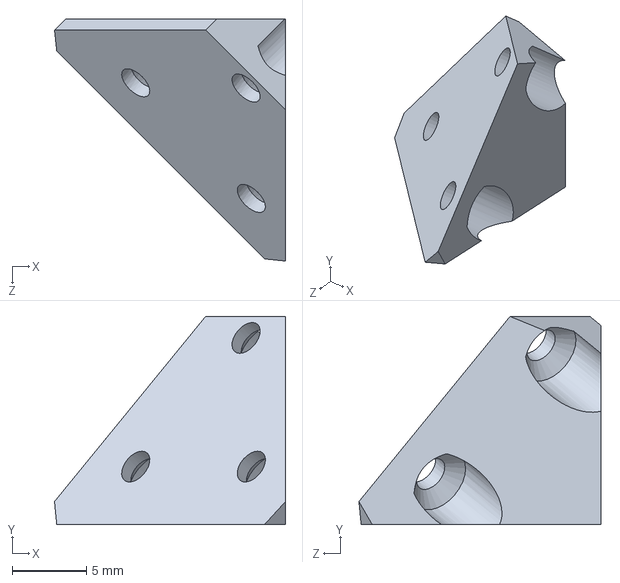
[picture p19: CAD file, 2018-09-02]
wedge.SLDPRT
15.5 x 14.0 x 16.3 mm

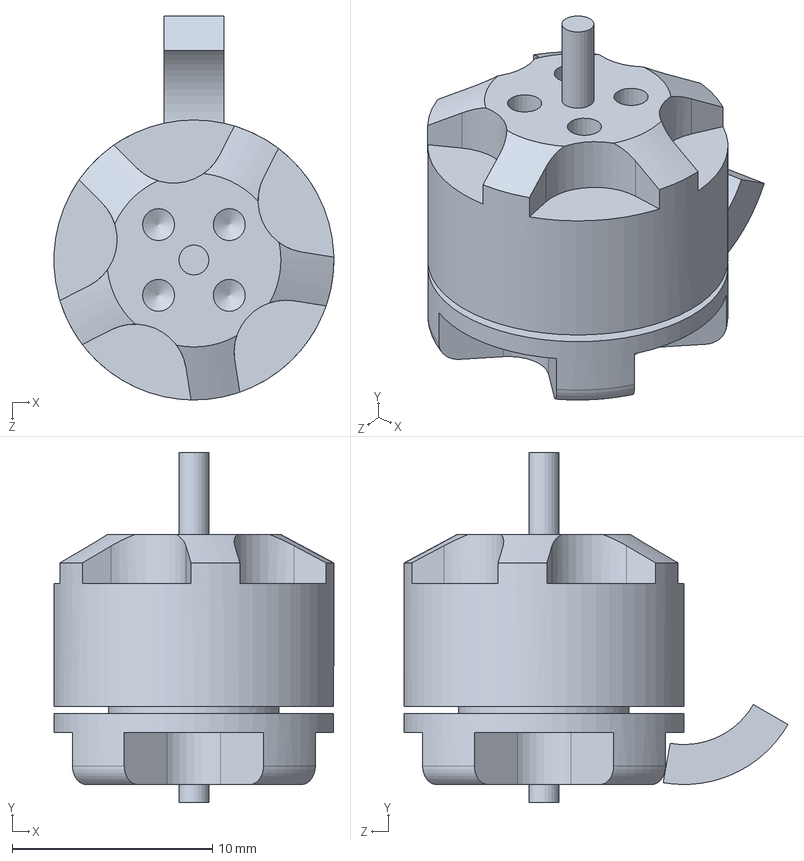
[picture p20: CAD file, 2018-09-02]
D1104-4000KV_rough.SLDPRT
14.0 x 17.5 x 19.2 mm

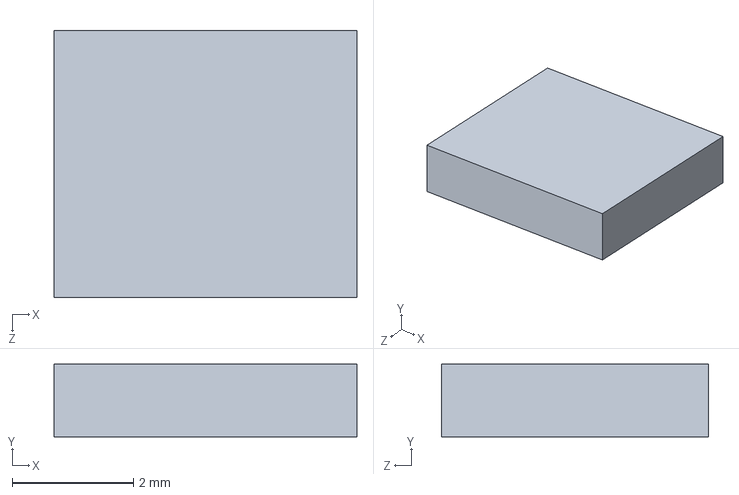
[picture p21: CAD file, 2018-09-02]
sensorStandin.SLDPRT
5.00 x 1.20 x 4.40 mm

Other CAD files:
magnet.SLDPRT
motorBracket_cage.SLDPRT
wedge_cage.SLDPRT
pilotGeometry.SLDPRT
COTS/M2x0.4x4_2x3shoulderScrew_90263A111_316 STAINLESS STEEL PRECISION SHOULDER SCREW.SLDPRT
COTS/M2x0.4x4_3x3shoulderScrew_90263A112_316 STAINLESS STEEL PRECISION SHOULDER SCREW.SLDPRT
COTS/M2x0.4x4_flatHead_hex_91294A002_BLACK ALLOY STEEL FLAT-HEAD SOCKET CAP SCREW.SLDPRT
COTS/M2x0.4x4_flatHead_phillips_91698A200_METRIC 18-8 SS FLAT HEAD PHIL MACHINE SCREW.SLDPRT
COTS/M2x0.4x5_buttonHead_91239A701_CLASS 10.9 STL BUTTON-HEAD SOCKET CAP SCREW.SLDPRT
COTS/M2x0.4x5_flatHead_torx_92703A144_STAINLESS STEEL TORX FLAT HEAD SCREWS.SLDPRT
COTS/M2x0.4x6_flatHead_hex_brass_97595A277_BRASS HEX DRIVE FLAT HEAD SCREW.SLDPRT
COTS/No2-56_ultra-lowShoulderScrew_90318A101_ULTRA-LOW-PROFILE PRECISION SHOULDER SCREW.SLDPRT
M2.5x0.45x4_flatHex_91294A473_BLK-OXIDE ALLOY STL HEX DRIVE FLAT HEAD SCREW.SLDPRT
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

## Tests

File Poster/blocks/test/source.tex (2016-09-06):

\documentclass[slidestop,compress]{beamer}
\usepackage[orientation=portrait,size=custom, width=25, height=8, debug]{beamerposter}
\usefonttheme{serif}
\usepackage{beamerthemeshadow}
\usepackage{beamerouterthemedefault}
\usepackage{amsmath,amssymb,amsthm}
\usenavigationsymbolstemplate{}
\usepackage[latin1]{inputenc}
\usepackage[catalan]{babel}
\usetheme{Copenhagen}\usetheme{Copenhagen}
\begin{document}
\begin{frame}[plain]
\begin{block}{OreSat}
-Mission
\end{block}
\end{frame}
\end{document}

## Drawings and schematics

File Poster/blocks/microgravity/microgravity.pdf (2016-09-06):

0.5 1

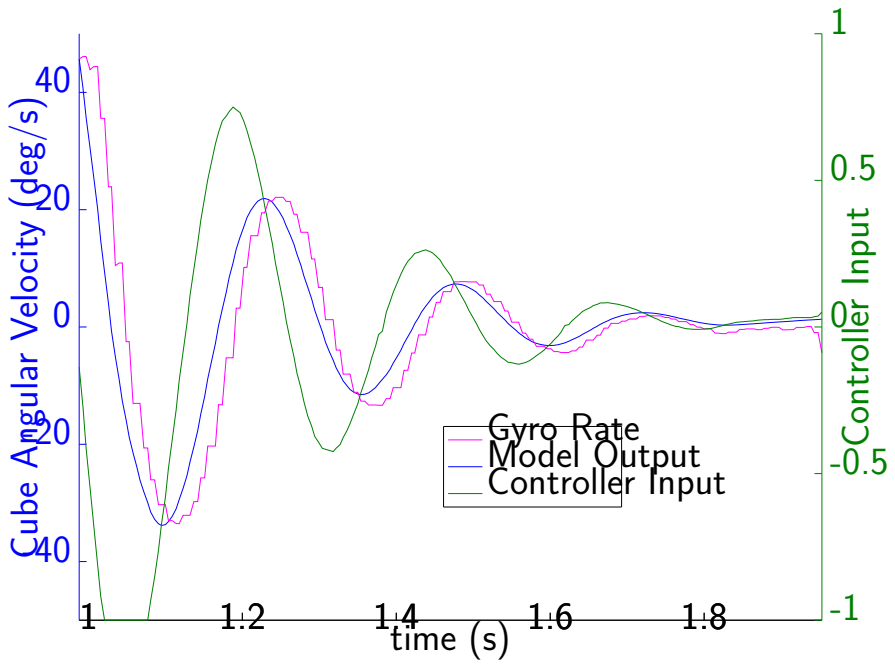
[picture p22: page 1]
time (s); Gyro Rate; Controller Input; Model Output Controller Input

Cube Angular Velocity (deg/s)

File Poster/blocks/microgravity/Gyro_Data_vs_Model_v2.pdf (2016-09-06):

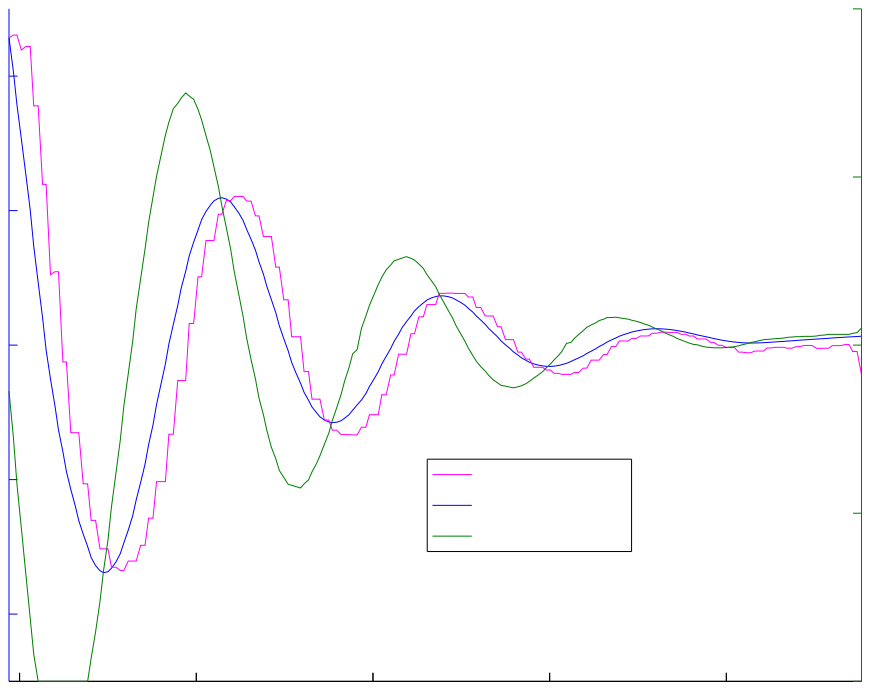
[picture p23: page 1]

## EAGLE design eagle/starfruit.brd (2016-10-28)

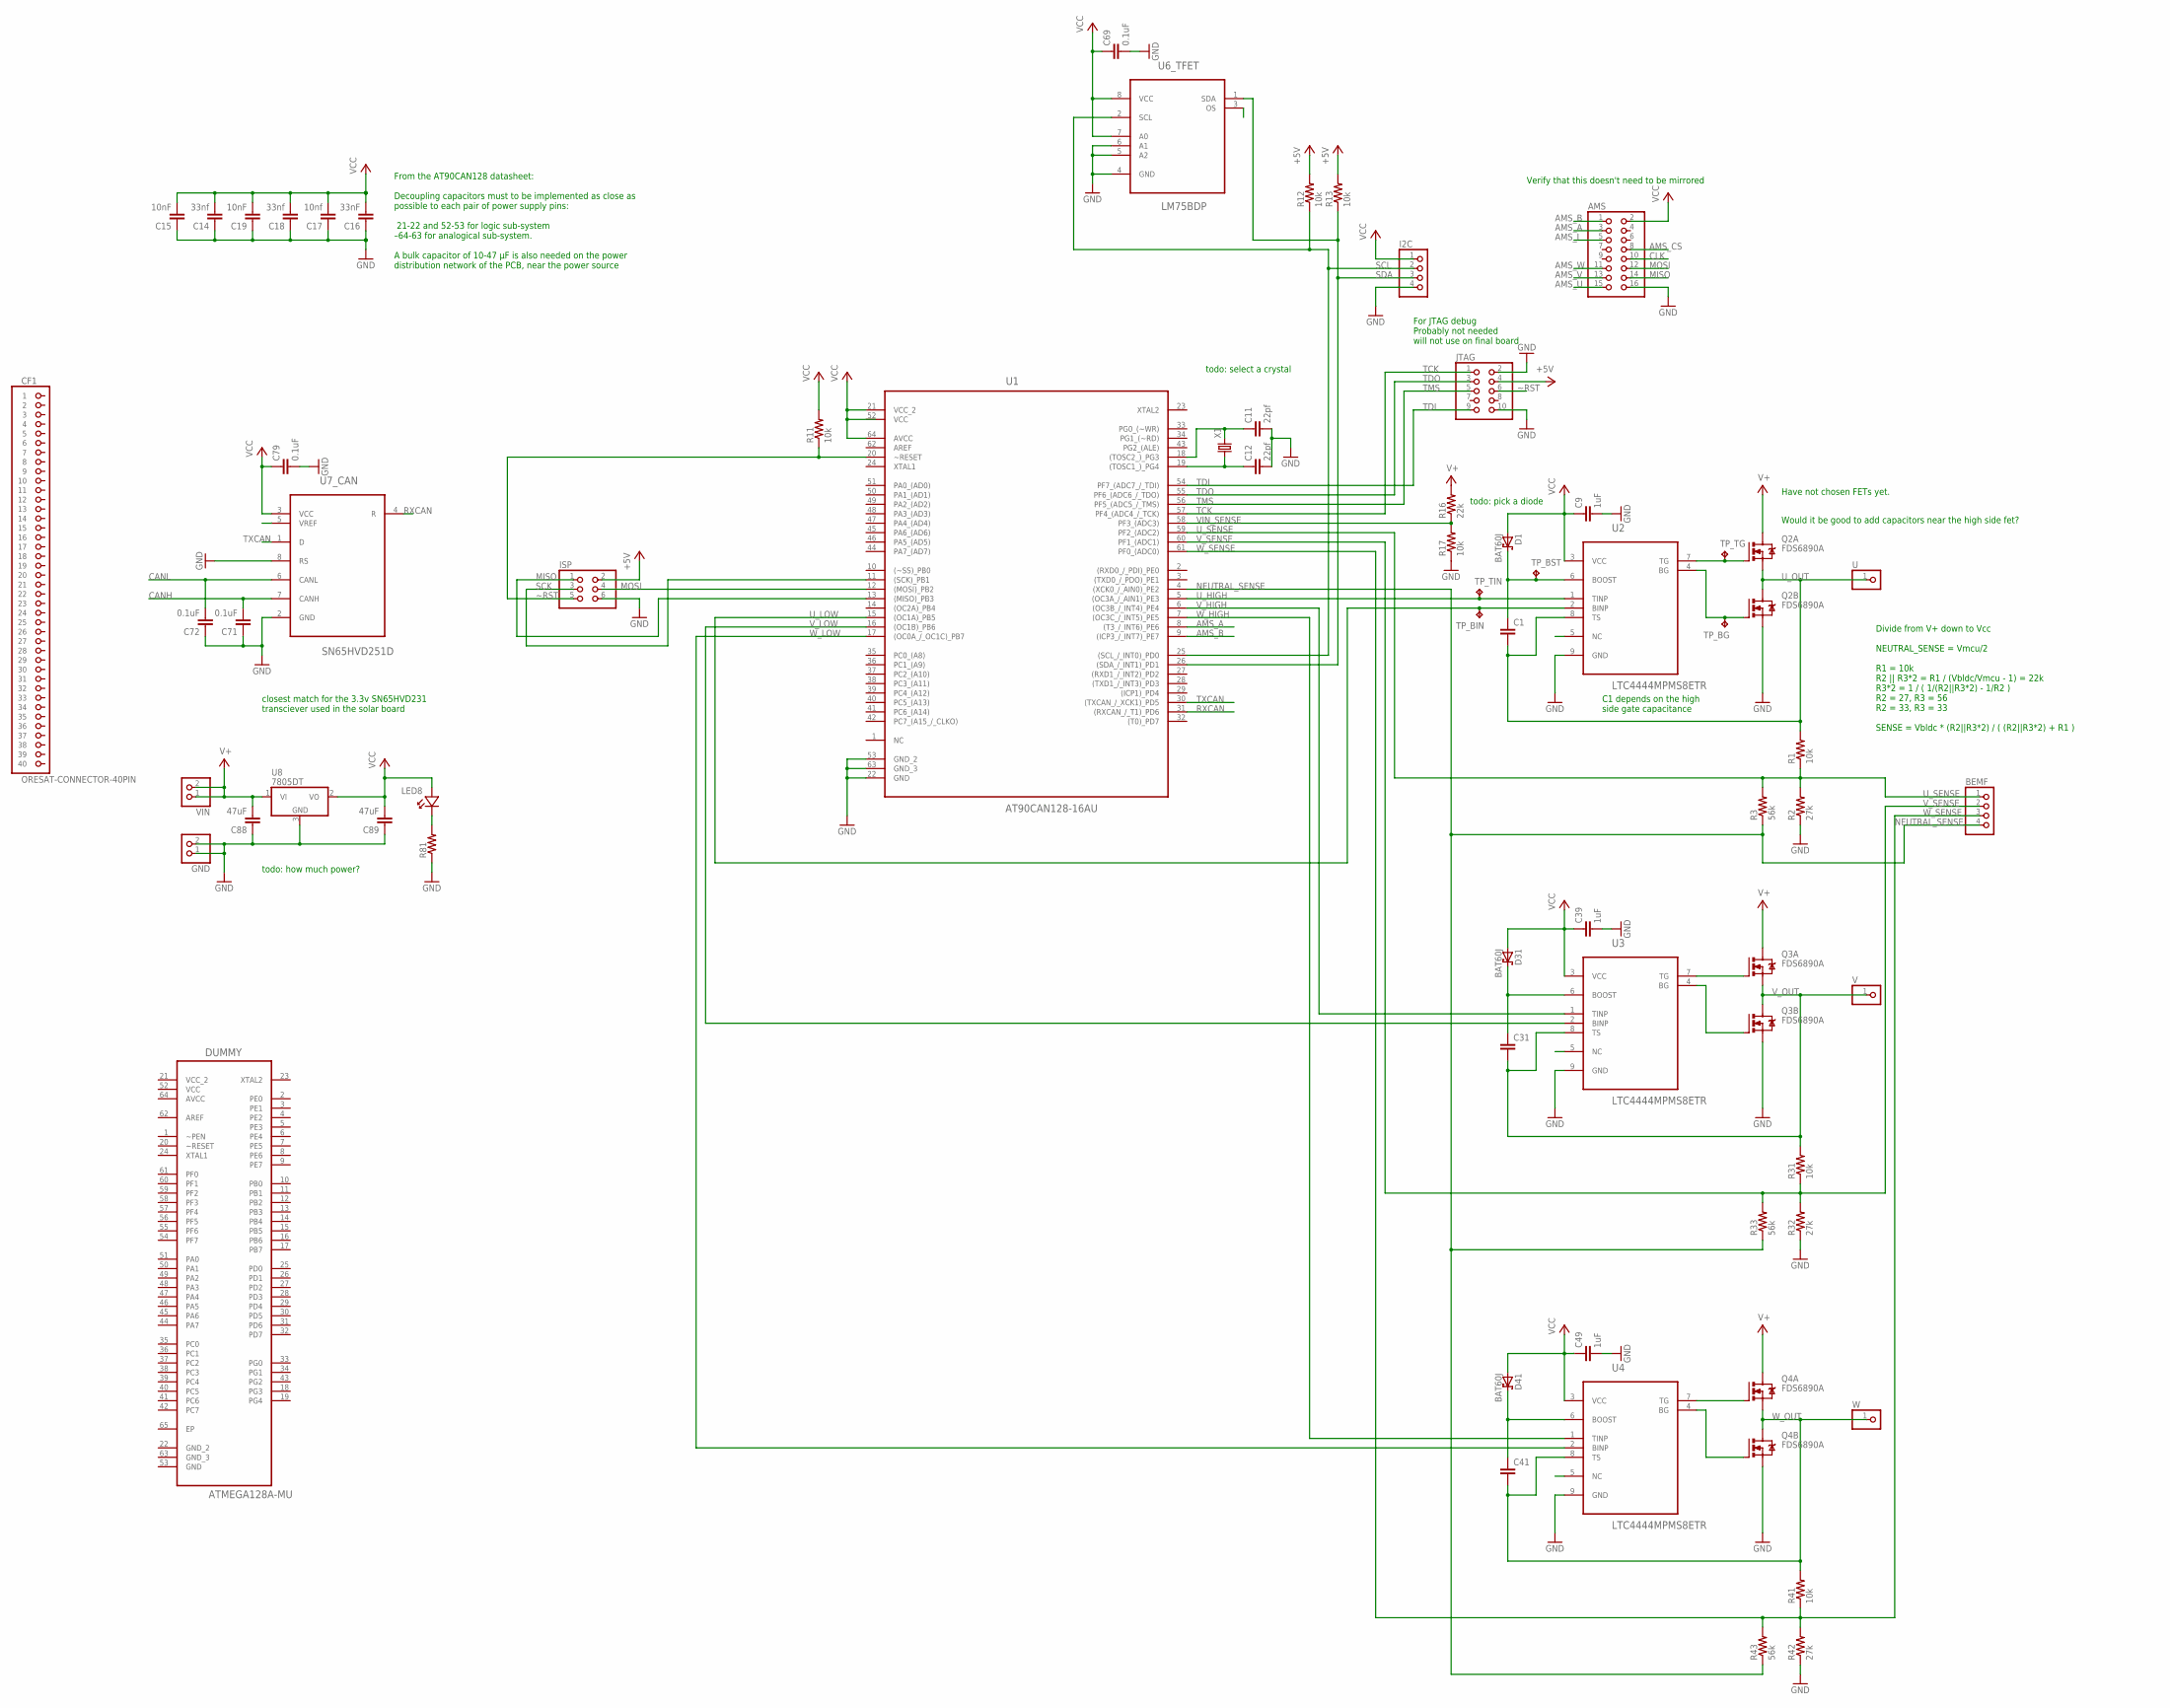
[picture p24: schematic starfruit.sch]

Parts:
AMS: PINHD-2X8; 2X08
BEMF: PINHD-1X4; 1X04
C1, C31, C41: C-EU0603-B-NOSILK; .0603-B-NOSILK
C9, C39, C49: 1uF; .0603-B-NOSILK
C11, C12: 22pf; .0603-B-NOSILK
C14, C18: 33nf; .0603-B-NOSILK
C15, C19: 10nF; .0603-B-NOSILK
C16: 33nF; .0603-B-NOSILK
C17: 10nf; .0603-B-NOSILK
C69, C71, C72, C79: 0.1uF; .0603-B-NOSILK
C88, C89: 47uF; .0603-B-NOSILK
CF1: ORESAT-CONNECTOR-40PIN; HARWIN-ARCHER-M50-3202045
D1, D31, D41: BAT60J; SOD323_ST
DUMMY: ATMEGA128A-MU; QFN50P900X900X100-65N
GND: PINHD-1X2; 1X02
I2C: PINHD-1X4; 1X04
ISP: PINHD-2X3; 2X03
JTAG: PINHD-2X5; 2X05
LED8: LED-0603
Q2, Q3, Q4: FDS6890A; M08A
R1, R11, R12, R13, R17, R31, R41: 10k; .0603-B-NOSILK
R2, R32, R42: 27k; .0603-B-NOSILK
R3, R33, R43: 56k; .0603-B-NOSILK
R16: 22k; .0603-B-NOSILK
R81: R-US_0603-B-NOSILK; .0603-B-NOSILK
TP_BG: TPTP06R; TP06R
TP_BIN: TPTP06R; TP06R
TP_BST: TPTP06R; TP06R
TP_TG: TPTP06R; TP06R
TP_TIN: TPTP06R; TP06R
U: PINHD-1X1; 1X01
U1: AT90CAN128-16AU; QFP80P1600X1600X120-64N
U2, U3, U4: LTC4444MPMS8ETR; SOP65P490X110-9N
U6_TFET: LM75BDP; SOP65P490X110-8N
U7_CAN: SN65HVD251D; SOIC127P600X175-8N
U8: 7805DT; TO252
V: PINHD-1X1; 1X01
VIN: PINHD-1X2; 1X02
W: PINHD-1X1; 1X01
X1: CRYSTALCTS406; CTS406

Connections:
AMS_A: AMS.3, U1.8 ((T3_/_INT6)_PE6)
AMS_B: AMS.1, U1.9 ((ICP3_/_INT7)_PE7)
AMS_CS: AMS.8
AMS_I: AMS.5
AMS_U: AMS.15
AMS_V: AMS.13
AMS_W: AMS.11
AVCC: DUMMY.64 (AVCC)
C79: C79.2
CANH: C71.2, U7_CAN.7 (CANH)
CANL: C72.2, U7_CAN.6 (CANL)
CLK: AMS.10
GND: AMS.16, C9.2, C11.2, C12.2, C14.1, C15.1, C16.1, C17.1, C18.1, C19.1, C39.2, C49.2, C69.2, C71.1, C72.1, C88.1, C89.1, GND.1, GND.2, I2C.4, ISP.6, JTAG.2, JTAG.10, Q2.3 (S), Q3.3 (S), Q4.3 (S), R2.1, R17.1, R32.1, R42.1, R81.1, U1.22 (GND), U1.53 (GND_2), U1.63 (GND_3), U2.9 (GND), U3.9 (GND), U4.9 (GND), U6_TFET.4 (GND), U6_TFET.5 (A2), U6_TFET.6 (A1), U7_CAN.2 (GND), U7_CAN.8 (RS), U8.3 (GND)
MISO: AMS.14, ISP.1, U1.13 ((MISO)_PB3)
MOSI: AMS.12, ISP.4, U1.12 ((MOSI)_PB2)
unnamed: LED8.K, R81.2
NEUTRAL_SENSE: BEMF.4, R3.1, R33.1, R43.1, U1.4 ((XCK0_/_AIN0)_PE2)
RXCAN: U1.31 ((RXCAN_/_T1)_PD6), U7_CAN.4 (R)
SCK: ISP.3, U1.11 ((SCK)_PB1)
SCL: I2C.2, R12.1, U1.25 ((SCL_/_INT0)_PD0), U6_TFET.2 (SCL)
SDA: I2C.3, R13.1, U1.26 ((SDA_/_INT1)_PD1), U6_TFET.1 (SDA)
TCK: JTAG.1, U1.57 (PF4_(ADC4_/_TCK))
TDI: JTAG.9, U1.54 (PF7_(ADC7_/_TDI))
TDO: JTAG.3, U1.55 (PF6_(ADC6_/_TDO))
TMS: JTAG.5, U1.56 (PF5_(ADC5_/_TMS))
TOSC1: C12.1, U1.19 ((TOSC1_)_PG4), X1.1
TOSC2: C11.1, U1.18 ((TOSC2_)_PG3), X1.3 (2)
TXCAN: U1.30 ((TXCAN_/_XCK1)_PD5), U7_CAN.1 (D)
T_BG: Q3.4 (G), U3.4 (BG)
U2_BOOST: C1.1, D1.C, TP_BST.TP, U2.6 (BOOST)
U2_NC: U2.5 (NC)
U3_BOOST: C31.1, D31.C, U3.6 (BOOST)
U3_NC: U3.5 (NC)
U4_BOOST: C41.1, D41.C, U4.6 (BOOST)
U4_NC: U4.5 (NC)
U6_NC: U6_TFET.3 (OS)
U7_NC: U7_CAN.5 (VREF)
U_BG: Q2.4 (G), TP_BG.TP, U2.4 (BG)
U_HIGH: TP_TIN.TP, U1.5 ((OC3A_/_AIN1)_PE3), U2.1 (TINP)
U_LOW: TP_BIN.TP, U1.15 ((OC1A)_PB5), U2.2 (BINP)
U_OUT: C1.2, Q2.1 (S), Q2.5 (D), Q2.6 (D), R1.2, U.1, U2.8 (TS)
U_SENSE: BEMF.1, R1.1, R2.2, R3.2, U1.59 (PF2_(ADC2))
U_TG: Q2.2 (G), TP_TG.TP, U2.7 (TG)
V+: C88.2, Q2.7 (D), Q2.8 (D), Q3.7 (D), Q3.8 (D), Q4.7 (D), Q4.8 (D), R16.2, U8.1 (VI), VIN.1, VIN.2
VCC: AMS.2, C9.1, C14.2, C15.2, C16.2, C17.2, C18.2, C19.2, C39.1, C49.1, C69.1, C79.1, C89.2, D1.A, D31.A, D41.A, DUMMY.52 (VCC), I2C.1, ISP.2, JTAG.4, LED8.A, R11.2, R12.2, R13.2, U1.21 (VCC_2), U1.52 (VCC), U1.64 (AVCC), U2.3 (VCC), U3.3 (VCC), U4.3 (VCC), U6_TFET.7 (A0), U6_TFET.8 (VCC), U7_CAN.3 (VCC), U8.2 (VO)
VCC_2: DUMMY.21 (VCC_2)
VIN_SENSE: R16.1, R17.2, U1.58 (PF3_(ADC3))
V_HIGH: U1.6 ((OC3B_/_INT4)_PE4), U3.1 (TINP)
V_LOW: U1.16 ((OC1B)_PB6), U3.2 (BINP)
V_OUT: C31.2, Q3.1 (S), Q3.5 (D), Q3.6 (D), R31.2, U3.8 (TS), V.1
V_SENSE: BEMF.2, R31.1, R32.2, R33.2, U1.60 (PF1_(ADC1))
V_TG: Q3.2 (G), U3.7 (TG)
W_BG: Q4.4 (G), U4.4 (BG)
W_HIGH: U1.7 ((OC3C_/_INT5)_PE5), U4.1 (TINP)
W_LOW: U1.17 ((OC0A_/_OC1C)_PB7), U4.2 (BINP)
W_OUT: C41.2, Q4.1 (S), Q4.5 (D), Q4.6 (D), R41.2, U4.8 (TS), W.1
W_SENSE: BEMF.3, R41.1, R42.2, R43.2, U1.61 (PF0_(ADC0))
W_TG: Q4.2 (G), U4.7 (TG)
~RST: ISP.5, JTAG.6, R11.1, U1.20 (~RESET)

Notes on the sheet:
From the AT90CAN128 datasheet: Decoupling capacitors must to be implemented as close as possible to each pair of power supply pins: 21-22 and 52-53 for logic sub-system –64-63 for analogical sub-system. A bulk capacitor of 10-47 µF is also needed on the power distribution network of the PCB, near t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
Divide from V+ down to Vcc NEUTRAL_SENSE = Vmcu/2 R1 = 10k R2 || R3*2 = R1 / (Vbldc/Vmcu - 1) = 22k R3*2 = 1 / ( 1/(R2||R3*2) - 1/R2 ) R2 = 27, R3 = 56 R2 = 33, R3 = 33 SENSE = Vbldc * (R2||R3*2) / ( (R2||R3*2) + R1 )
For JTAG debug Probably not needed will not use on final board
C1 depends on the high side gate capacitance
Have not chosen FETs yet.
Verify that this doesn't need to be mirrored
closest match for the 3.3v SN65HVD231 transciever used in the solar board
todo: select a crystal
todo: how much power?
Would it be good to add capacitors near the high side fet?
todo: pick a diode

Board: 2 copper layers, 67 parts (0 on the bottom side), 45 nets, no tracks yet.

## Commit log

2016-10-15 expanded a bit on torques
2016-10-21 solidworks model for AMS eval board
    [ams5147_adapter_board.SLDPRT, ams5147_adapter_board.STL]
2018-05-08 prototype of reaction wheel mounting
    [motorBracket.SLDPRT, pilotGeometry.SLDPRT, wedge.SLDPRT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]
2018-05-09 prototyping for the D1104... then SW crashed
    [D1104-4000KV_rough.SLDPRT, motorBracket.SLDPRT, wedge.SLDPRT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]
2018-05-09 finished draft of encoder board for D1104
    [encoderBoard.SLDDRW, encoderBoard.sldprt, motorBracket.SLDPRT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]
2018-05-10 fancified the motor mount
    [D1104-4000KV_rough.SLDPRT, M2.5x0.45x4_flatHex_91294A473_BLK-OXIDE ALLOY STL HEX DRIVE FLAT HEAD SCREW.SLDPRT, encoderBoard.sldprt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]
2018-05-10 extended board further; fixed CSK holes on wedge
    [encoderBoard.SLDDRW, encoderBoard.sldprt, motorBracket.SLDPRT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]
2018-05-29 other-handed version of the wedge
    [encoderBoard.sldprt, motorBracket.SLDPRT, wedgeDefinition.SLDASM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]
2018-06-07 tweaked wedge to work with structure
    [pilotGeometry.SLDPRT, wedge.SLDPRT, wedgeDefinition.SLDASM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]
2018-06-07 more uniform assembly scheme
    [wedge.SLDPRT, wedge_enantio.SLDPRT, wheelUnit.SLDASM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]
2018-06-10 added materials for calculating CoM
    [D1104-4000KV_rough.SLDPRT, encoderBoard.sldprt, motorBracket.SLDPRT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]
2018-06-10 intermediate mounting scheme for reaciton wheels
    A small C-beam mounts to the structure and the wedges mount to the beam.
    This allows us to tweak the position -- and the entire mounting scheme
    -- of the reaction wheels without needing to re-machine the entire
    structure!
    [mountingBeam.SLDASM, mountingBeam.SLDPRT, mountingExample.SLDASM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]
2018-06-11 tweaked wedge locations to symmetrize encoders
    [mountingBeam.SLDPRT]
2018-07-30 approximate details of motor model based on their drawing
    [D1104-4000KV_rough.SLDPRT]
2018-07-30 new revision of the reaction wheels; needs tweaking
    [M2x0.4x4_shoulderScrew_2mm_90263A111_316 STAINLESS STEEL PRECISION SHOULDER SCREW.SLDPRT, M2x0.4x5_buttonHead_91239A701_CLASS 10.9 STL BUTTON-HEAD SOCKET CAP S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]
2018-08-13 removed files from previous revision
    [encoderBoard.SLDDRW, encoderBoard.sldprt, motorBracket.SLDPRT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]
2018-08-13 renamed things for new revision appropriately
    [encoderBoard.SLDPRT, motorBracket.SLDPRT, wedge.SLDPRT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]
2018-08-13 updated mounting beam assembly
    [D1104-4000KV_rough.SLDPRT, M2.5x0.45x4_flatHex_91294A473_BLK-OXIDE ALLOY STL HEX DRIVE FLAT HEAD SCREW.SLDPRT, M2x0.4x5_buttonHead_91239A701_CLASS 10.9 STL BUT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]
2018-08-13 wonky double wheel unit...? (got rid of it)
    [mountingBeam.SLDASM, wheelUnit.SLDASM]
2018-09-02 re-tweaked wheel and cage dimensions
    [M2x0.4x4_flatHead_hex_91294A002_BLACK ALLOY STEEL FLAT-HEAD SOCKET CAP SCREW.SLDPRT, M2x0.4x4_flatHead_phillips_91698A200_METRIC 18-8 SS FLAT HEAD PHIL MACHINE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]
2018-09-02 made the cage shear-able
    [motorBracket.SLDPRT, wheel.SLDPRT, wheelUnit.SLDASM]
2018-09-02 optimized to fit in 3 slots; materials and colors
    [D1104-4000KV_rough.SLDPRT, M2x0.4x6_flatHead_hex_brass_97595A277_BRASS HEX DRIVE FLAT HEAD SCREW.SLDPRT, encoderBoard.SLDPRT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]
2018-09-16 created technical drawing of the reaction wheel
    [wheel.SLDDRW]
2018-09-23 finalized ACS board and provided DXF/drawing
    [M2x0.4x4_2x3shoulderScrew_90263A111_316 STAINLESS STEEL PRECISION SHOULDER SCREW.SLDPRT, No2-56_ultra-lowShoulderScrew_90318A101_ULTRA-LOW-PROFILE PRECISION SH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]
2018-10-07 added thermal contacts to the ACS board
    [encoderBoard.DXF, encoderBoard.SLDDRW, encoderBoard.SLDPRT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]
2018-12-03 updated mounting beam
    [encoderBoard.SLDPRT, mountingBeam.SLDASM, mountingBeam.SLDPRT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]
2019-02-25 fixed shoulder screw, mounting beam discrepancies
    [M2x0.4x4_2x3shoulderScrew_90263A111_316 STAINLESS STEEL PRECISION SHOULDER SCREW.SLDPRT, M2x0.4x4_3x3shoulderScrew_90263A112_316 STAINLESS STEEL PRECISION SHOU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]
2019-02-25 added recent tweaks to the encoder board drawing
    [encoderBoard.SLDDRW, encoderBoard.SLDPRT]
2019-02-25 alignment tweaks on RW and cap
    [magnetCap.SLDDRW, magnetCap.SLDPRT, wheel.SLDDRW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]
2019-02-25 added missing fasteners; encoder board DXF
    [M2x0.4x5_flatHead_torx_92703A144_STAINLESS STEEL TORX FLAT HEAD SCREWS.SLDPRT, encoderBoard.DXF, mountingBeam.SLDASM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]
